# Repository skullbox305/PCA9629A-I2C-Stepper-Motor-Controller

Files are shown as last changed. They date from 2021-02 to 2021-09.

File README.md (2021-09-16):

# PCA9629A I²C Stepper Motor Controller Breakout Board 

- ## Features

  - NXP PCA9629A I²C Stepper Controller
  - Allegro A3909 Dual Full Bridge Motor Driver
  - Maxim Integrated MAX17291 5.5V Boost Converter powering the controller and motor (can be deselected through a jumper to power a motor up to 18V)

- ## ToDo
  - Boost converter is very weak. Replace for another with higher current.

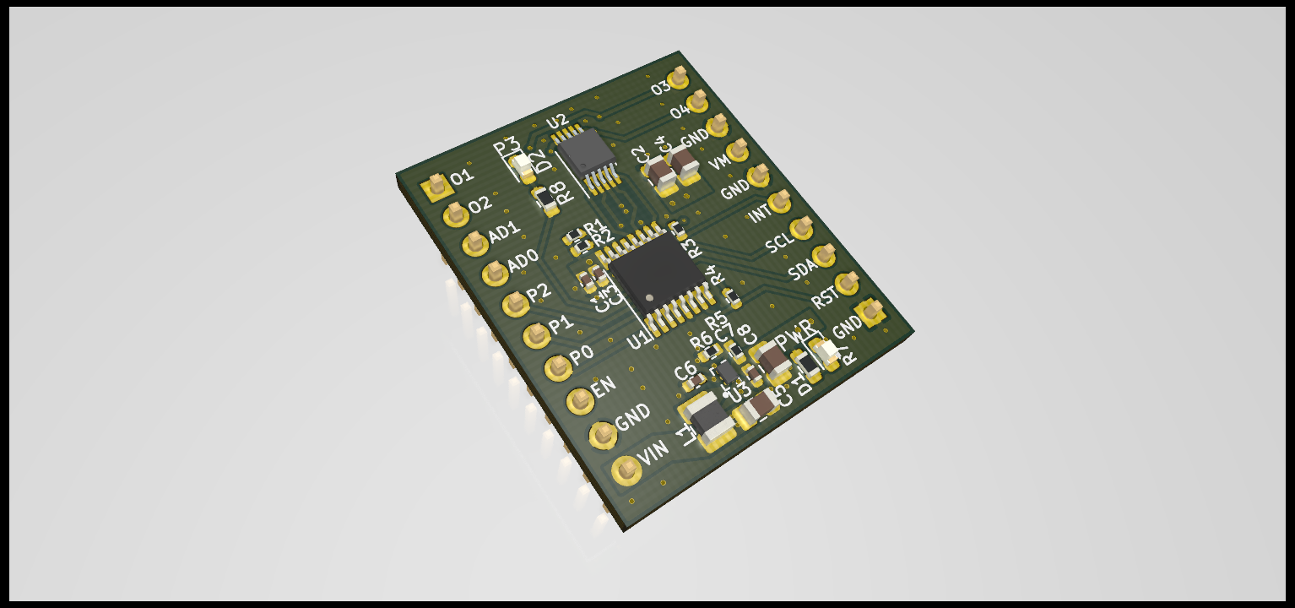
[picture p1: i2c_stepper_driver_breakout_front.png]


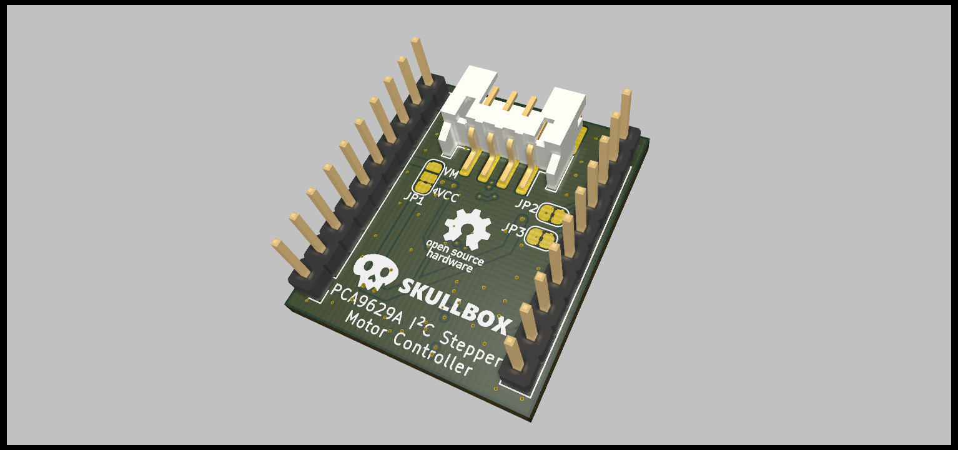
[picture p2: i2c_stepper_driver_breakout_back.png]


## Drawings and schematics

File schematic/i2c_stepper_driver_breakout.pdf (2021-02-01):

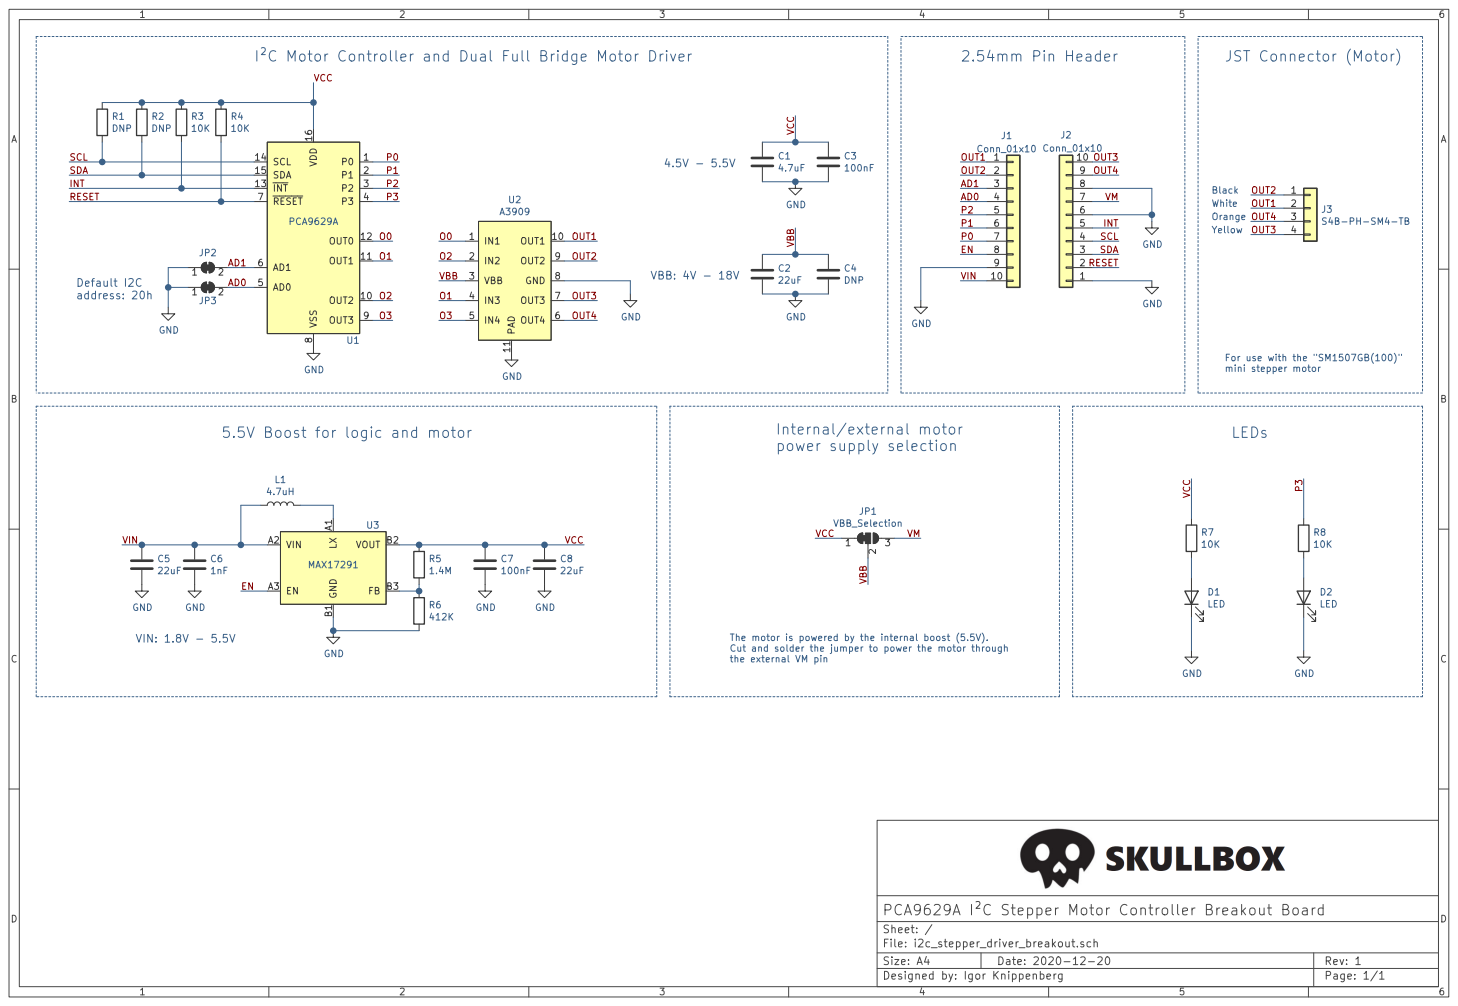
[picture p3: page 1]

mini stepper motor White Orange Yellow

For use with the "SM1507GB(100)"

The motor is powered by the internal boost (5.5V).
Cut and solder the jumper to power the motor through
the external VM pin

PCA9629A I²C Stepper Motor Controller Breakout Board
File: i2c_stepper_driver_breakout.sch Sheet: /

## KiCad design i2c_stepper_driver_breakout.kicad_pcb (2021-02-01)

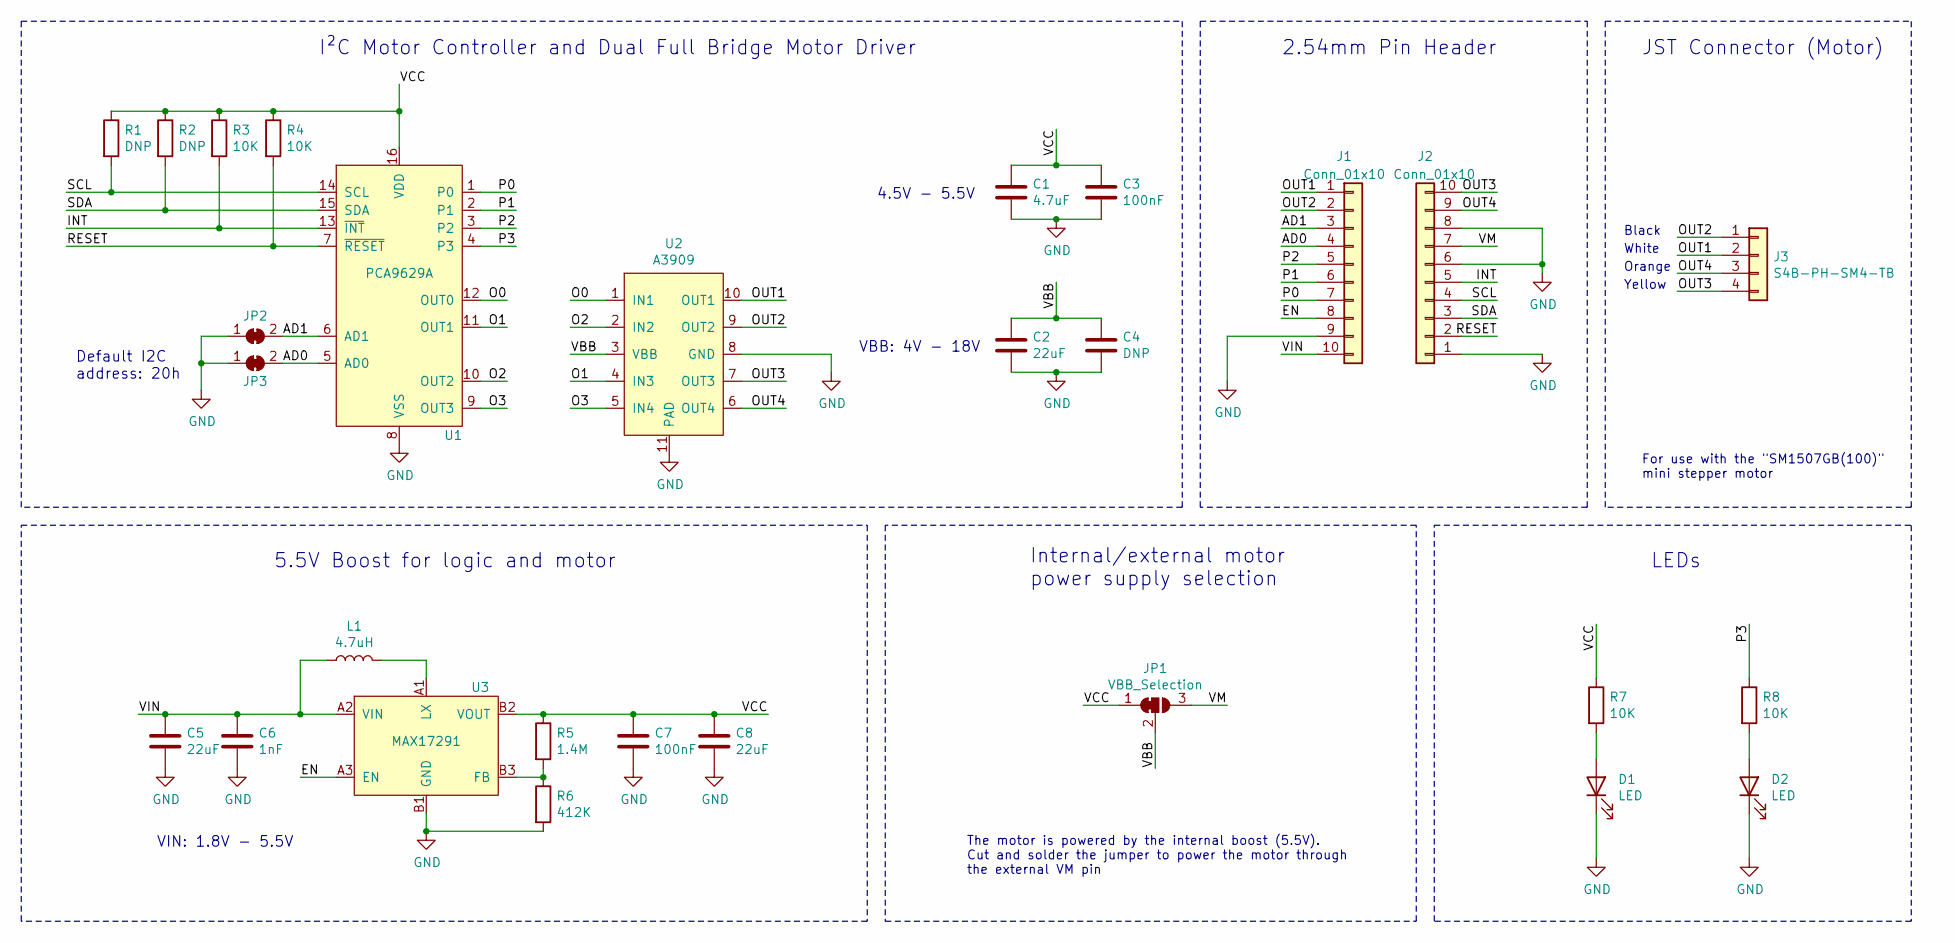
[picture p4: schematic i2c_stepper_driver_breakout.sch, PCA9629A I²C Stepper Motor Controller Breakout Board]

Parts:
C1: 4.7uF; C_0402_1005Metric; MPN C1005X5R1A475K050BC
C2, C5, C8: 22uF; C_0805_2012Metric; MPN CL21A226MAYNNNE
C3, C7: 100nF; C_0402_1005Metric; MPN GCM155R71C104JA55D
C4: DNP; C_0805_2012Metric
C6: 1nF; C_0402_1005Metric; MPN 0402YC102KAT2A
D1, D2: LED; LED_0603_1608Metric; MPN LS L29K-G1H2-1-Z
J1, J2: Conn_01x10; PinHeader_1x10_P2.54mm_Vertical
J3: S4B-PH-SM4-TB; JST_PH_S4B-PH-SM4-TB_1x04-1MP_P2.00mm_Horizontal; MPN S4B-PH-SM4-TB(LF)(SN)
JP1: VBB_Selection; SolderJumper-3_P1.3mm_Bridged2Bar12_RoundedPad1.0x1.5mm
JP2, JP3: SolderJumper_2_Bridged; SolderJumper-2_P1.3mm_Bridged2Bar_RoundedPad1.0x1.5mm
L1: 4.7uH; L_1008_2520Metric; MPN LQH2HPZ4R7MGRL
R1, R2: DNP; R_0402_1005Metric
R3, R4: 10K; R_0402_1005Metric; MPN RC0402FR-0710KL
R5: 1.4M; R_0402_1005Metric; MPN RK73H1ETTP1404F
R6: 412K; R_0402_1005Metric; MPN ERJ-2RKF4123X
R7, R8: 10K; R_0603_1608Metric; MPN AC0603JR-0710KL
U1: PCA9629A; TSSOP-16_4.4x5mm_P0.65mm; MPN PCA9629APWJ
U2: A3909; MPN A3909GLYTR-T
U3: MAX17291; MAX17291ATA+; MPN MAX17291ANT+

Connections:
/AD0: J1.4, JP3.2 (B), U1.5 (AD0)
/AD1: J1.3, JP2.2 (B), U1.6 (AD1)
/EN: J1.8, U3.A3 (EN)
/INT: J2.5, R3.2, U1.13 (~INT)
/O0: U1.12 (OUT0), U2.1 (IN1)
/O1: U1.11 (OUT1), U2.4 (IN3)
/O2: U1.10 (OUT2), U2.2 (IN2)
/O3: U1.9 (OUT3), U2.5 (IN4)
/OUT1: J1.1, J3.2, U2.10 (OUT1)
/OUT2: J1.2, J3.1, U2.9 (OUT2)
/OUT3: J2.10, J3.4, U2.7 (OUT3)
/OUT4: J2.9, J3.3, U2.6 (OUT4)
/P0: J1.7, U1.1 (P0)
/P1: J1.6, U1.2 (P1)
/P2: J1.5, U1.3 (P2)
/P3: R8.1, U1.4 (P3)
/RESET: J2.2, R4.2, U1.7 (~RESET)
/SCL: J2.4, R1.2, U1.14 (SCL)
/SDA: J2.3, R2.2, U1.15 (SDA)
/VBB: C2.1, C4.1, JP1.2 (C), U2.3 (VBB)
/VCC: C1.1, C3.1, C7.1, C8.1, JP1.1 (A), R1.1, R2.1, R3.1, R4.1, R5.1, R7.1, U1.16 (VDD), U3.B2 (VOUT)
/VIN: C5.1, C6.1, J1.10, L1.1, U3.A2 (VIN)
/VM: J2.7, JP1.3 (B)
GND: C1.2, C2.2, C3.2, C4.2, C5.2, C6.2, C7.2, C8.2, D1.1 (K), D2.1 (K), J1.9, J2.1, J2.6, J2.8, JP2.1 (A), JP3.1 (A), R6.2, U1.8 (VSS), U2.8 (GND), U2.11 (PAD), U3.B1 (GND)
unnamed: D1.2 (A), R7.2
unnamed: D2.2 (A), R8.2
unnamed: L1.2, U3.A1 (LX)
unnamed: R5.2, R6.1, U3.B3 (FB)

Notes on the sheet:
Default I2C address: 20h
2.54mm Pin Header
4.5V - 5.5V
VBB: 4V - 18V
I²C Motor Controller and Dual Full Bridge Motor Driver
JST Connector (Motor)
5.5V Boost for logic and motor
The motor is powered by the internal boost (5.5V). Cut and solder the jumper to power the motor through the external VM pin
VIN: 1.8V - 5.5V
Black
LEDs
Internal/external motor power supply selection
For use with the "SM1507GB(100)" mini stepper motor
White
Orange
Yellow

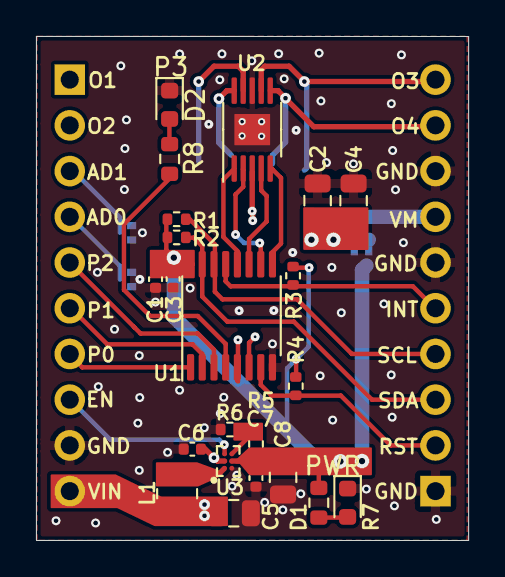
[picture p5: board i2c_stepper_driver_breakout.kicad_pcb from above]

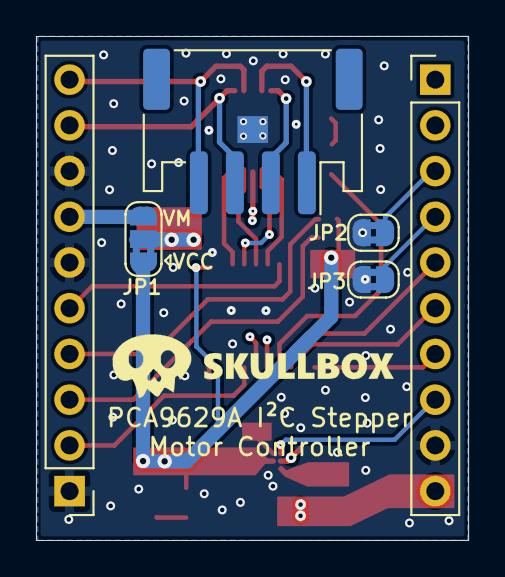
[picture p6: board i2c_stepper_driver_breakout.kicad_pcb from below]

Board: 4 copper layers, 24.0 x 28.0 mm, 28 parts (6 on the bottom side), 28 nets.

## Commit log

2020-12-17 Started schematic and Layout
    [i2c_stepper_driver_breakout.kicad_pcb, i2c_stepper_driver_breakout.sch]
2020-12-18 Continued layout
    [i2c_stepper_driver_breakout.kicad_pcb, i2c_stepper_driver_breakout.sch]
2020-12-19 Added boost converter, continued layout
    [i2c_stepper_driver_breakout.kicad_pcb, i2c_stepper_driver_breakout.sch]
2020-12-20 Finished schematic and layout for now
    [i2c_stepper_driver_breakout.kicad_pcb, i2c_stepper_driver_breakout.sch]
2021-02-01 Layout modifications due to some bugs
    h
    [i2c_stepper_driver_breakout.kicad_pcb, i2c_stepper_driver_breakout.sch]
